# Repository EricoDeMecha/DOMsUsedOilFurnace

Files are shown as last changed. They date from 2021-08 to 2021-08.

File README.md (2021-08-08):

## DOMs: Design of a used oil furnace

Design of a used oil furnace from a mechatronics perspective. This is an improvement of what already exist and is based on the following research and implementation
## Basic description

- Pressurized oil flows through a nozzle.
- It is ignited at first and then burns on its own.
- Supercharger(Externally driven by a motor) can be added to maximize combustion.
- Ignition can be shifted from manual ignition to the use of gasoline+diesel mixture for ignition.
- Oil can be preheated also for maximum combustion

## Objectives

- High strength, and high temperature material for the design of the nozzle.(Oil atomizer)
- Automatic controlled flow of the oil.
- Automatic ignition.
- Design of a supercharger for maximum combustion(Miniblower).
- Automatic pressurizing of oil(regulator).
- Oil pre-heating
- Automatic switch over from diesel+gasoline ignition to oil burning independently.
- Smoke handling.(carbonmonoxide and smoke detectors)
- **Safety**

## Proposed designs

- Ignition system
- Nozzle
- Burning chamber
- preheating chamber

{Oil conveyance system}
## References

**Evolved used oil furnace**

Evolved used oil furnace implementation (https://www.youtube.com/watch?v=s_Ad897si6g&list=PLajok_EjFfbOb4fP-WGI7LOqIf2R0RhqM)

**Incredible burner**

Evolved used oil furnace implementation (https://www.youtube.com/watch?v=8lF8vNczoqE&list=PLajok_EjFfbMtI4L1jHQWJG012ae7ZYwm)

**JKUAT Masters Research paper**

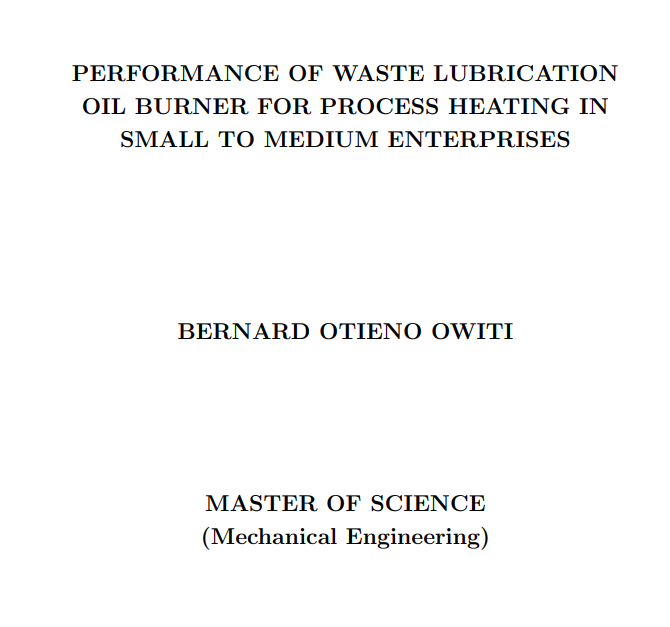
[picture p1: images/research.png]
Used oil furnace research (http://ir.jkuat.ac.ke/bitstream/handle/123456789/1776/OWITI%20B.%20O.%20MSc.%202015.pdf?sequence=1&isAllowed=y)


## Findings and miscelleneous  section
1. Miscelleneous

According to this guy here with his bad boy ...

Material evidence (https://www.youtube.com/watch?v=Qnzh19kDVuw)

* He has hit 1834 degrees by using silicon carbide in the burner and nozzle.
* He is using a thermal gun for temperature measurement and not the usual temperature industrial probe.
* Design of the nozzle
* Running at 3L/hr
* Design- simple design(Nozzle has blade with it, the blade closes the burner and can detached easily)
* Burner is also surrounded with another metal sheet to tap and direct more air directly to the flame.

2. Applications

* House warming during winter.
* Metal smelting.

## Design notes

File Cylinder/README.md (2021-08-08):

# Cylinder modelling
Modelling the cylinder thickness using internal pressure, ultimate tensile strength and factor of safety 

Installing and compiling with matplotlibcpp

## Setup

```bash
    sudo apt-get install python-pip # install pip for python 2.7
    sudo pip2 install matplotlib  # install matplotlib for python 2.7
    sudo pip2 install numpy 
    sudo apt-get install python-tk # installing tkinter for python 2.7
```

## Usage

```bash
    mkdir build  &&  g++ ../cylinderThickness.cpp  -I/usr/include/python2.7 -I/usr/local/lib/python2.7/dist-packages/numpy/core/include -lpython2.7 && ./a.out
```

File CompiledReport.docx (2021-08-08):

Conventional Oil Furnaces

Burner

Conventional designs of the burner do not gather for its maintainability. The burner is designed as a single solid attached to the nozzle. Since most furnaces operate at temperatures more than 1800⁰C, such burners burn out and become non-functional after some few operations. Due to the solid design of such furnaces, replacements of such parts require overhauling. The choice of material plays a role in the frequency of maintenance.

Nozzle

Most designs use separate nozzles for pressurized air and oil. Such a design has proven to be inefficient since smoke emissions are frequently witnessed. It also introduces complexity in the design since the pressurized air nozzle has to be placed as the measured distance from the pressurized oil nozzle and this might not always be accurate.

Ignition

Ignition for conventional oil furnaces employs a flammable burner mounted on an insulator or even soaked in a highly flammable petroleum fuel. This method is unsafe since its control is limited. The use of highly flammable petroleum fuel for ignition also makes it expensive and borderline dangerous.

Emission

Combustion of oil in a good proportion of oxygen produces carbon dioxide. During oxygen deficiencies, carbon monoxide is released. If not detected and controlled such gases can be catastrophic. Since such emissions are invisible, conventional designs of this type of furnace do not gather for such hazards.

Oil Consumption

Conventional designs are based on the workability of the design. Its efficiency is rather given very minimal attention. The use of separate nozzles for the pressurized oil and air undermines the efficiency of the design. As such, the consumption of oil is rather higher.

Assembly

Processes

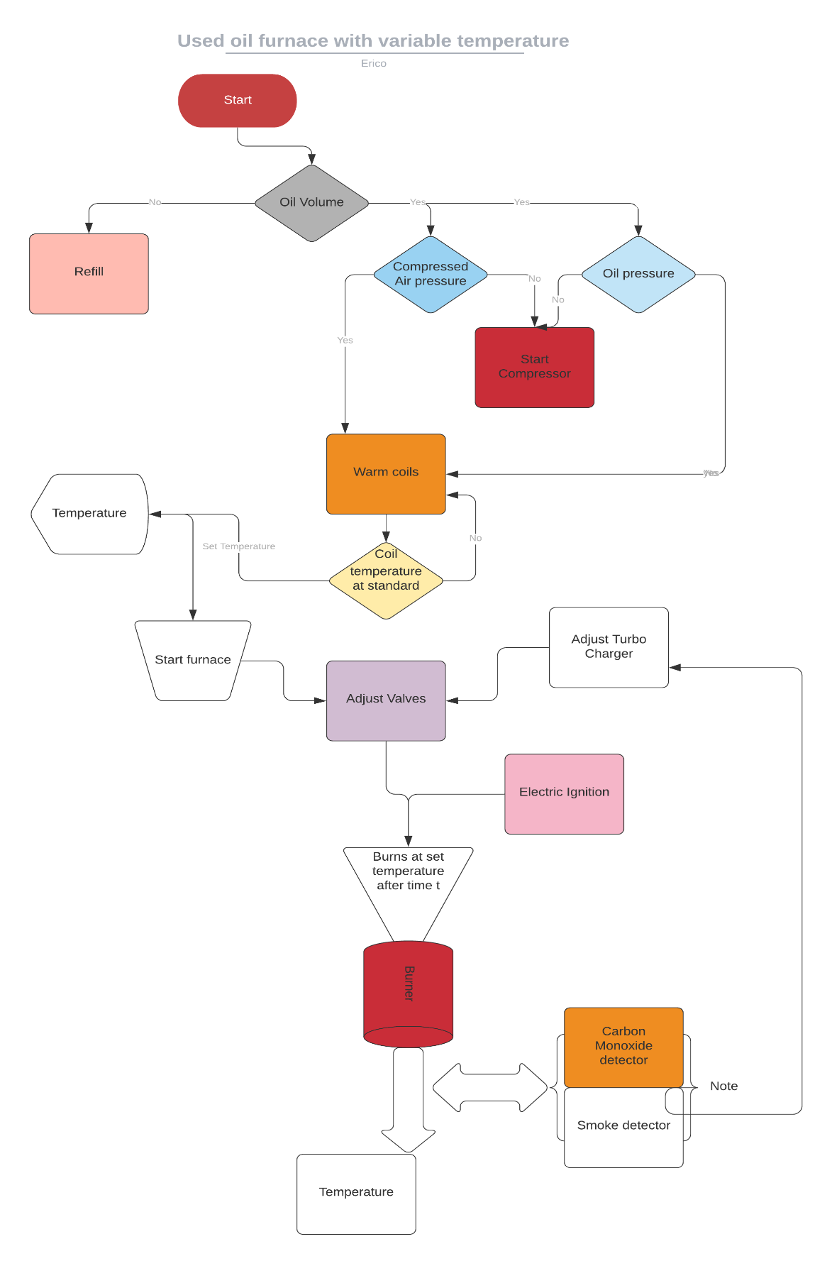
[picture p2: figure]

On powering on, the system automatically checks the volume of oil in the oil storage tank. This is determined by a level sensor installed in the tank. Depending on the volume, the system decides whether to refill the tank from an even bigger tank or raise an alert for a refill. If the required volume of oil is available the system then checks the pressure of oil in the tank and the pressure of compressed air in the air storage tank using pressure sensors. In any case, the pressure is below the required, the system automatically turns on the compressor to refill the two containers to the required pressure. Once the pressure requirements in the two containers are met, the system automatically switches off the compressors and starts warming the coils on the path of the pressurized oil to the injector. The compressor is turned on, and off to maintain constant pressure in the tank.

Once the coils warm to a standard base temperature, the user is then prompted on the interface to enter the furnace operation temperature. From this input, the system adjusts both the air and pressurized oil valves using a stepper motor connected to each of the valves. A supercharger is connected to the compressed air flow pipe through a pneumatic motor and a pneumatic gear system to magnify the speed of the airflow. It is also adjusted in proportion to the pressure along the airflow pipe. This is to ensure the maximum supply of oxygen to the combustion chamber and to reduce emissions.

The pressurized oil and compressed air mix evenly in the coaxial swirl injector. The injector is designed in such a way that it ensures oil is atomized and mixes evenly with enough amounts of oxygen. Once the flow of oil and pressurized air is steady, an electric igniter descends to the tip of the nozzle and sparks to ignite the mixture. It then retracts to a safer height since its material cannot withstand furnace temperatures.

The mixture burns at the burner. With the correct choice of material, the burner can achieve up to 1834⁰C. Around the burner are the smoke detector, carbon monoxide detector, and a thermal gun. These sensors continuously check the smoke, levels of carbon monoxide, and temperature at the output, and this information is transferred to the ECU which adjusts the supercharger, oil, and air valves to correct the values.

Cylinder modeling

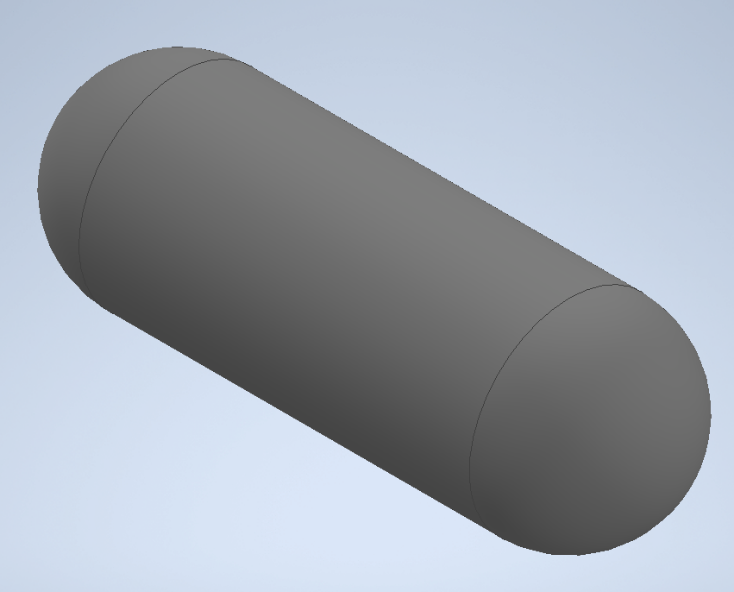
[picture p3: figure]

Fig 1.1 Cylinder

Thickness

The cylinder is designed to have to have the following dimensions:

Length: 3m

Internal Diameter: 800mm

The thickness of the cylinder has to be chosen carefully to achieve a recommended factor of safety for pressure vessels of between 3 and 6. To determine that, Clavarino’s equation is preferred to Lame’s equation since the cylinder is closed at both ends as shown in figure 1.1.

Clavarinos Equation

Clavarinos equation is used to determine the wall thickness of a cylinder. This is equation is applicable to cylinders with closed ends made of ductile materials. It is based on maximum principal strain theory.

Fig 1.2 Clavarinos Formula

Where:

P is the internal pressure, N/m²

D is the internal diameter, m

S is the allowable tensile stress, N/m²

t is the thickness of the material shell, m

µ is the poison’s ratio

Material

The material of the cylinder is chosen to meet the following objectives:

i. The material should be light (weight). This allows for bigger sizes without the limit of weight.
ii. It should be less rusty.
iii. Carbon content should not exceed a 1/8 of its total mass

Above objectives narrows down the search of the material to Carbon fiber or Fiber Glass. The amount of carbon in carbon fiber makes it a lesser attractive choice as compared to Fiber Glass even though it has a higher ultimate tensile strength. Fiber Glass is therefore chosen for the design of the cylinder.

Standard fiber glass has the following properties:

i. Ultimate tensile strength 1950-2000Mpa
ii. Poisson’s ration 0.23

Computing the ultimate thickness

To compute the ultimate thickness of the cylinder, the value of internal pressure of the cylinder can be assumed and the thickness computed. This method involves several guesses to obtain an ultimate internal pressure for a factor of safety of between 3 and 6.

Instead, a MATLAB script can be written to compute the ultimate internal pressure and thickness for a factor of safety between 3 and 6. The script is a shown below:

clc

clear

p_fos = 3; % recommended factor of safety for pressure vessels is between 3.0 - 6.0

D = 800; % internal diameter 800mm

S = 1950 * 10^6; % Ultimate tensile strength for Fiber glass

u = 0.23; % poissons ratio for fiber glass

t = [0,0.001]; % 1000th of a meter starting thickness

P = [0,0];

figure(1);

plot(P,t,"x");

i = 2;

while(1)

i = i+1;

% internal pressure

P(i)= (S*((((2*t(i-1)/D)+1)^2)-1))/((1-2*u)+(1+u)*(((2*t(i-1)/D)+1)^2));

t_fos = S/P(i); % factor of safety(fos)

% if fos is below the recommended value,break

if(t_fos < p_fos)

break

end

hold on

t(i)= t(i-1)+0.01; % 0.01 increment thickness

plot(P(1:i),t(1:i),"x");

end

title("Thickness against Internal Pressure")

ylabel("Thickness(m)");

xlabel("Pressure(Pa)")

legend("Shell Thickness vs internal pressure")

hold off

This script however, has a downside. The simulation involves computing more than 10,000 values for only a factor of safety below 30. MATLAB is super slow for this kind of computation.

An alternative C++ script can be written to speed up the computation. This is as shown below.

#include "matplotlibcpp.h"

#include <cmath>

namespace plt = matplotlibcpp;

int main(){

// declare constants

const int p_fos = 3; // recommended factor of safety for pressure vessels is between 3.0 - 6.0

const int D = 800; // internal diameter 800mm

const int S = (1950 * std::pow(10,6)); // Ultimate tensile strength for Fiber glass

const float u = 0.23; // poissons ratio for fiber glass

// prepare the data

std::vector<double> t,P;

t.emplace_back(0.001);// 1000th starting thickness

P.emplace_back(0);// 0 starting pressure

while(1){

double temp = (S*(std::pow(((2*t.back()/D)+1),2)-1))/((1-2*u)+(1+u)*std::pow(((2*t.back()/D)+1),2));

P.emplace_back(temp);

t.emplace_back((t.back() + 0.1));// increment thickness by 0.01

float _fos = (S / P.back()); // compute factor of safety

printf("%f\n",_fos);

if(_fos < 3){

break;

}

}

printf("Ultimate pressure: %f\n",P.back());

plt::figure_size(1300,768);

plt::named_plot("Thickness vs Internal pressure",P,t);

plt::title("Thickness Vs Internal pressure");

plt::legend();

plt::show();

}

The script computes both the internal pressure and factor of safety with varying thickness and stops when the factor of safety goes below 3. It then plot the relation between the thickness of the cylinder shell and the internal pressure. The plot is as shown below.

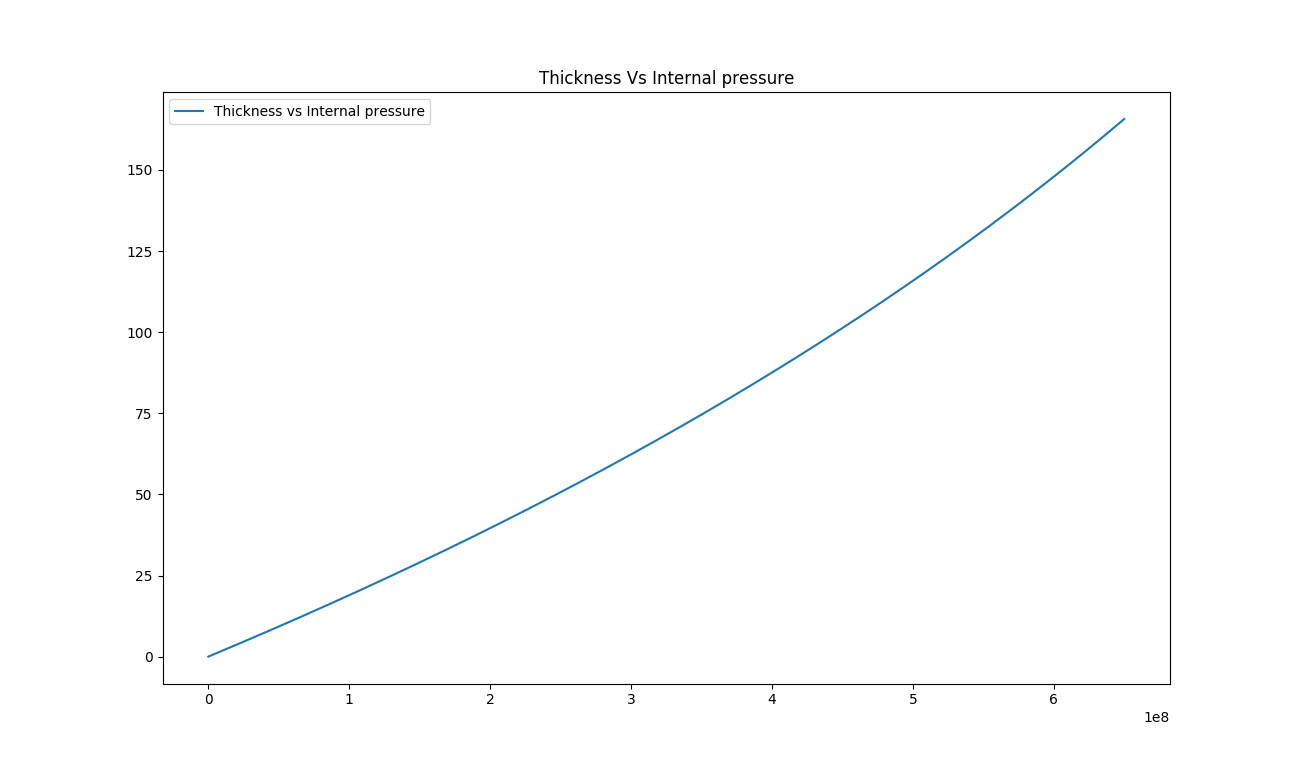
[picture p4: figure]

Fig 1.2 Thickness against Internal pressure

This shows that the relation between the internal pressure and the thickness of cylinder is linear. From the computation, it is also obtained that internal pressure of the cylinder for a factor of safety 3 is 650.042MPa. and thickness 42.075mm as shown below:

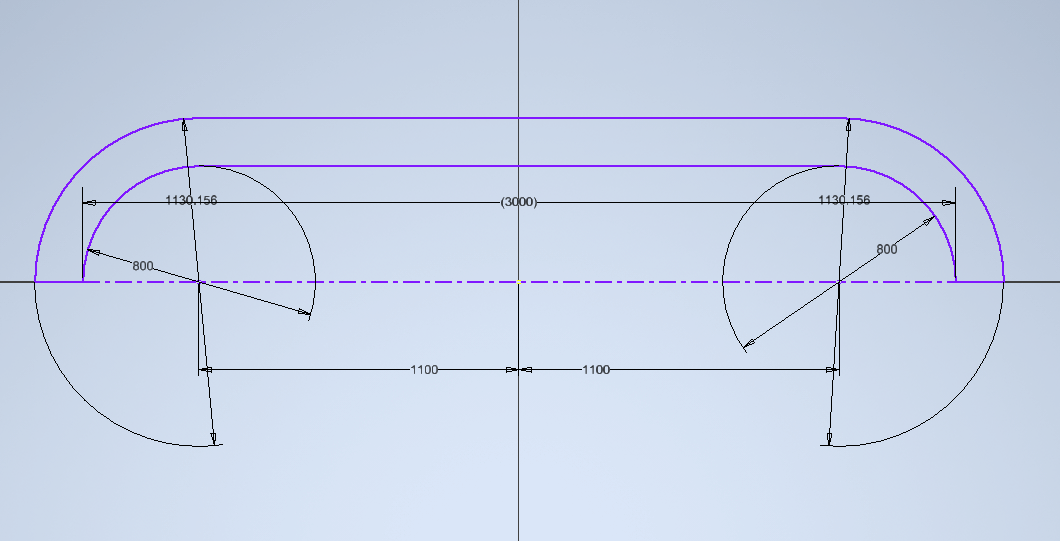
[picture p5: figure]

Fig 1.3 Actual dimensions of the cylinder

Atomizer

An atomizer is required to deliver the pressurized oil under high pressure to the combustion unit in a tiniest sprays possible. There are three viable designs for the atomizer: coaxial swirl injector, pintle injector and self-impinging injector. From the above designs the coaxial swirl injector was selected due its ease of fabrication compared to the pintle injector and self-impinging injector. The injector is expected to deliver the pressurized oil with ideal flow characteristics and atomize the fuel adequately.

Coaxial Swirl Injector

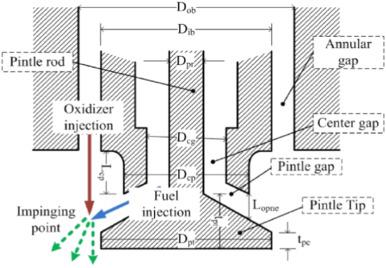
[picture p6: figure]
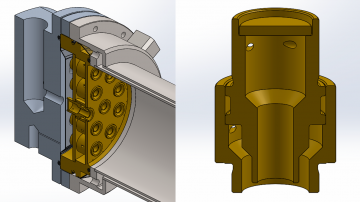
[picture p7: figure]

Fig 1,1 Coaxial Swirl Injector

Coaxial swirl injector performs the primary function of feeding oil to the combustion chamber. The design of this injector for oil furnace meets the following functional requirements;

1. The oil injector must be able to inject oil into the combustion chamber at the correct ratio and correct flow rates. For this reason the discharge coefficient of the injector must be determinable.
2. The oil injector should ensure complete mixing of oil with air to avoid undesired combustion with might result in the emission of carbon monoxide.
3. The oil injector must facilitate a primary pressure drop of between 10-20% to prevent discharged oil from flowing back into the injection system and causing an explosion.

Design

This swirl injector will consist of two primary parts; the inner element and the outer element. The two elements are placed on different levels separated by a separator plate. The inner element takes in pressurized oil tangentially which causes the liquid to swirl along the wall of the inner section. The pressurized oil enters the outer section tangentially as well and swirls along the wall of the outer element. This results in the pressurized air leaving the inner element in the shape of a cone which collides with the cone formed by the outer element. In this way the pressurized oil and pressurized air each leave each of the elements in a cylindrical manner colliding and atomizing due to the high pressure and velocity of the flow. The configuration is as displayed in figure 1.

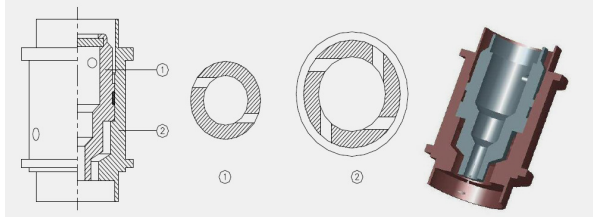
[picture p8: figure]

Fig 1.2 Swirl Injector Exploded View

This configuration meets the functional requirements of any fuel injector system .The efficiency of the injector for oil of any density can reach as high as 95%. The swirl injector has the following advantages;

1. The design is highly scalable since the assembly can be made bigger by adding the number of swirl elements in the assembly.
2. The swirl and assembly are relatively easy to machine
3. The swirl offers high atomization which is crucial for the conversion of chemical energy to thermal energy
4. The swirl element offers adjustable flow parameters allowing the assembly to create oxygen rich zones and oil rich zones.
5. Swirl elements offer the ability to vary the velocity of the fuel which can enhance the mixing of the pressurized air and pressurized oil.

The disadvantages of swirl injectors are:

1. They are a relatively new type of injector with fewer developed optimization characteristics
2. They require high dimensional accuracy for high performance

The other types of injector designs considered were;

Assembly and Fabrication

The development of the design was done by separating the assembly into five distinct parts:

1. Separator plate
2. Base plate
3. Swirler cap
4. Inner swirl element
5. Outer swirler element

Swirl Assembly

The parts were drawn on Autodesk Inventor for the 3D representation. The individual parts were then assembled. A cross section of the assembly is shown below.

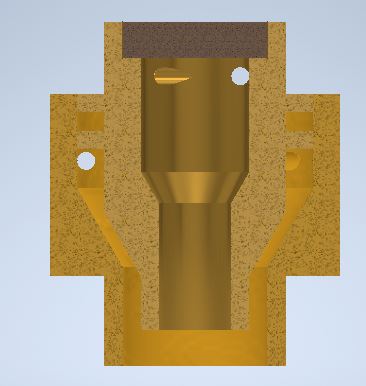
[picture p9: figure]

Fig 1.3 Cross section of the assembly

MasterCAM was then used to show the fabrication processes.

The cap was machined using a CNC lathe. The first process was facing the stock. This was followed by a rough surface turning on the outer diameter profile followed by a finishing process on the surface. The part was then cut off from the stock using a grooving tool. The tool paths are shown below:

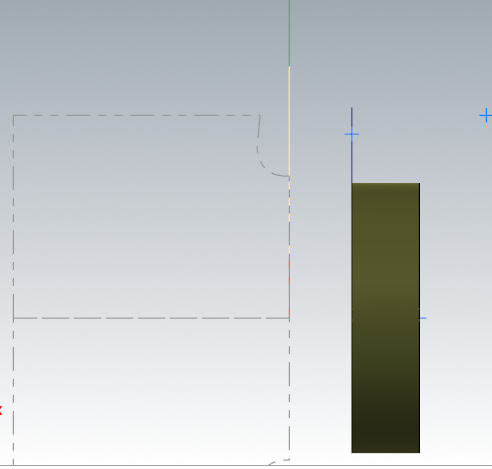
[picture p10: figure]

Fig 1.4 Cap Machining

The inner element was machined using a CNC lathe. The first process was facing using a right hand turning tool. A rough turning operation was then used to bring the dimensions to closer tolerance of the desired profile. A grooving operation was then used to machine the flanges on the profile. A grooving tool was also used to finish the tapered turning on the end of the part. A finishing turning operation was then done to bring the part to the required dimensions. A diameter 4 drill was then used to drill through the entire part. A diameter 8 drill was then used to a depth of 9mm. An internal grooving tool is then used to finalize the internal profile. The part was then cut off from the stock using a grooving tool. The holes were machined using a five axis milling machine. The figure below some of the generated tool paths.

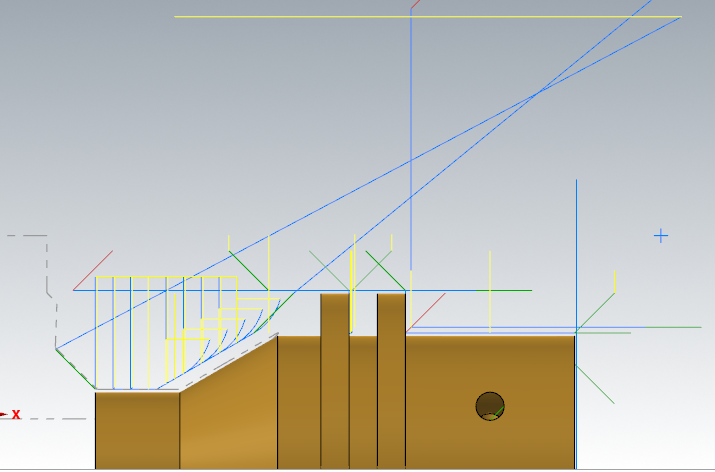
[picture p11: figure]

Fig 1.5 Inner element of the swirler

The outer element was machined using a CNC lathe. The first process was facing. This was followed by a rough turning operation on the profile. A grooving tool was then used to machine the end on the profile where there is a diameter change. The outer element was then finalized with a finishing turning operation. For the internal profile a drill of diameter 8 is passed through the entire stock. THis is followed by a drilling with a 12 mm drill to a depth of 12.12mm. The internal profile is then finalized by an internal turning operation. The part was then cut off from the stock using a grooving tool. The holes were machined using a 5 axis milling machine.

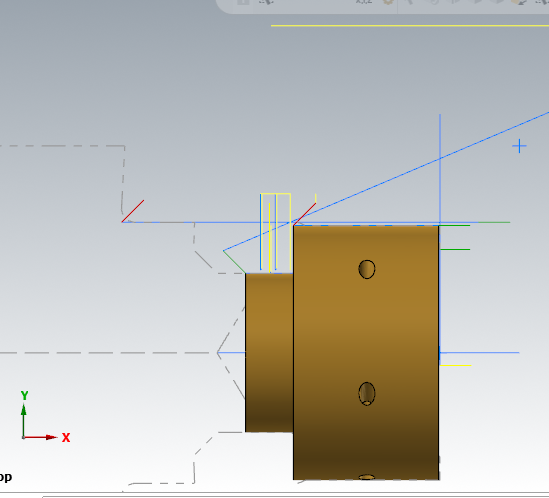
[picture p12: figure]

Fig 1.6 Outer element of the swirler

Base plate

The stock of this part was as defined:

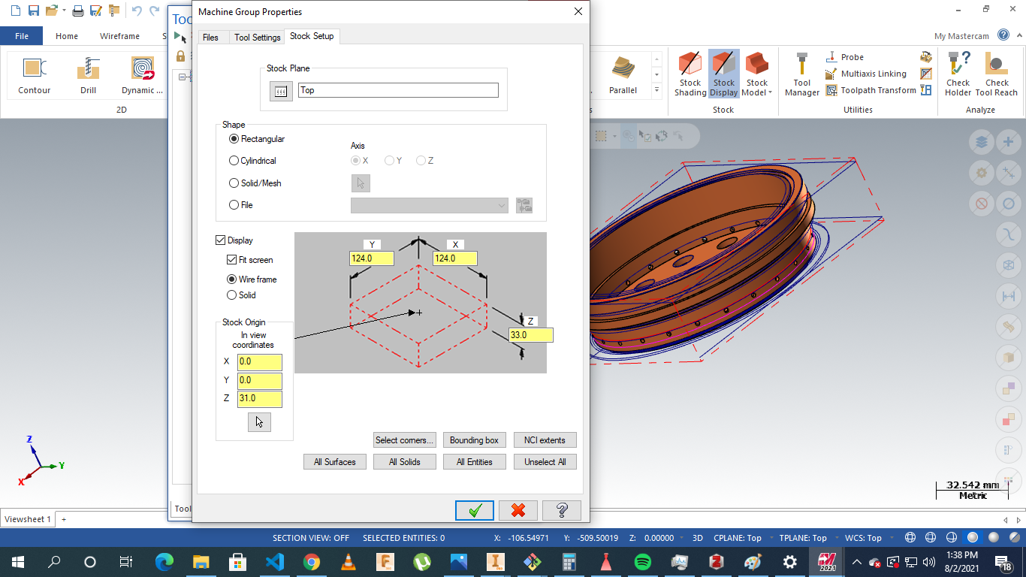
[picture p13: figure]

Fig 1.7 Base plate machining

The operations were to conducted on a five axis milling. The processes involved include: facing, contour milling drilling slot milling and multi-axis drilling.

The parts were milled as the material to be used was brass.

Operations are highlighted below:

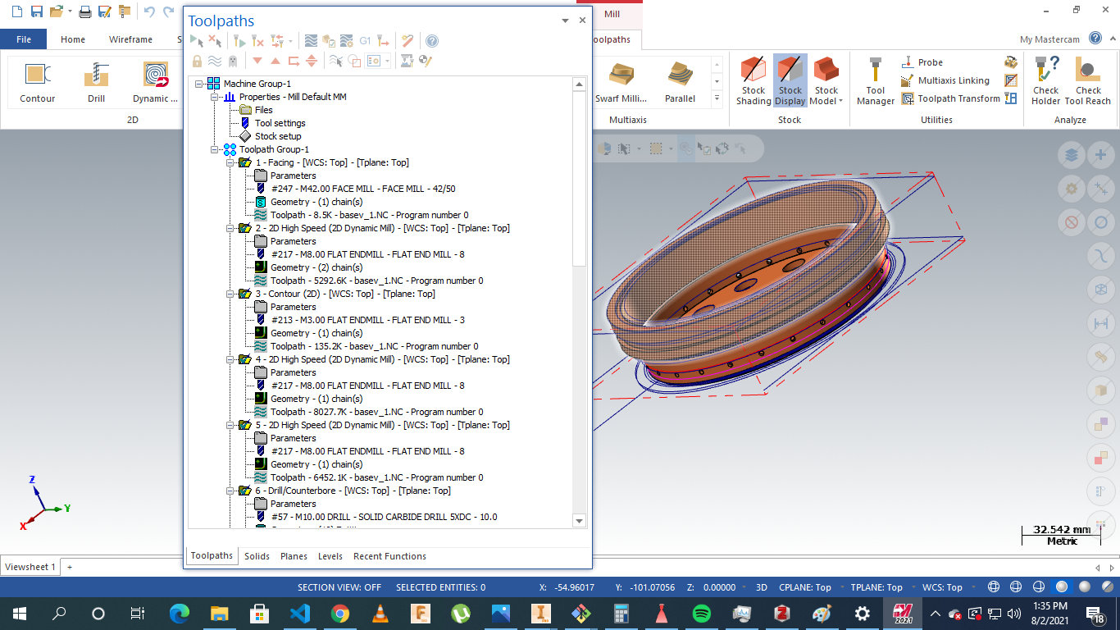
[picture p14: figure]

Fig 1.8 Base Plate total operations

Separator plate

The stock was as defined:

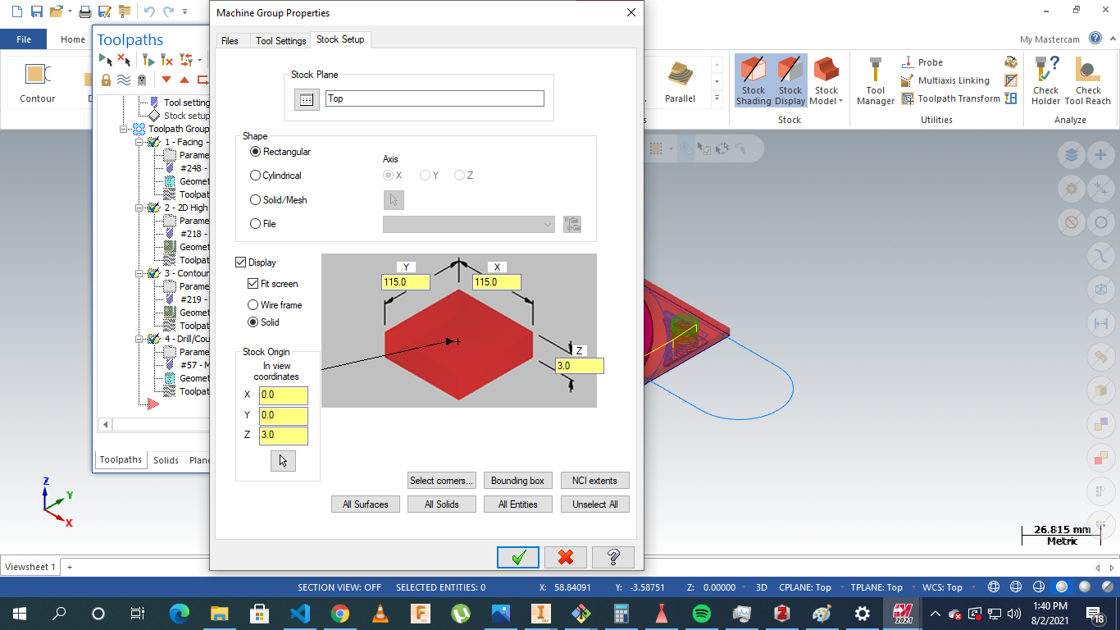
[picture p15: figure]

Fig 1.9 Separator plate stock Setup

The operations involved: facing, drilling,contouring and parting.

The processes were as displayed :

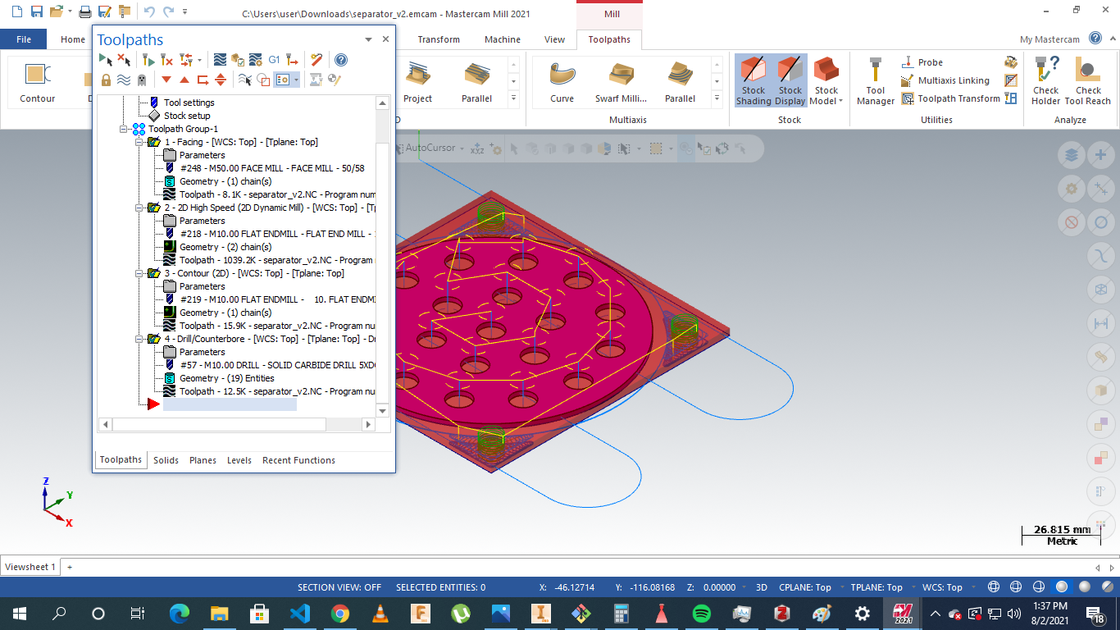
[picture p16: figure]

Fig 2.0 Stock Plate Machining Instructions

References

L.-J. Yang and Q.-F. Fu, ‘Theoretical Investigation on the Dynamics of a Gas-Liquid Coaxial Swirl Injector’, (https://www.zotero.org/google-docs/?tOBzsF)J. Propuls. Power (https://www.zotero.org/google-docs/?tOBzsF), vol. 27, no. 1, pp. 144–150, 2011. (https://www.zotero.org/google-docs/?tOBzsF)

H. Belal, A. Makled, and M. Al-Sanabawy, “Vaporization-controlled simplified model for liquid propellant rocket engine combustion chamber design,” IOP Conference Series: Materials Science and Engineering, vol. 610, p. 012088, Oct. 2019, doi: 10.1088/1757-899X/610/1/012088.

Edge, E. (2021). Clavarinos equation thick-walled cylinders of ductile material Calculator and formula. Retrieved 7 August 2021, from https://www.engineersedge.com/calculators/clavarinos_equation_thickwalled_cylinders_15620.htm

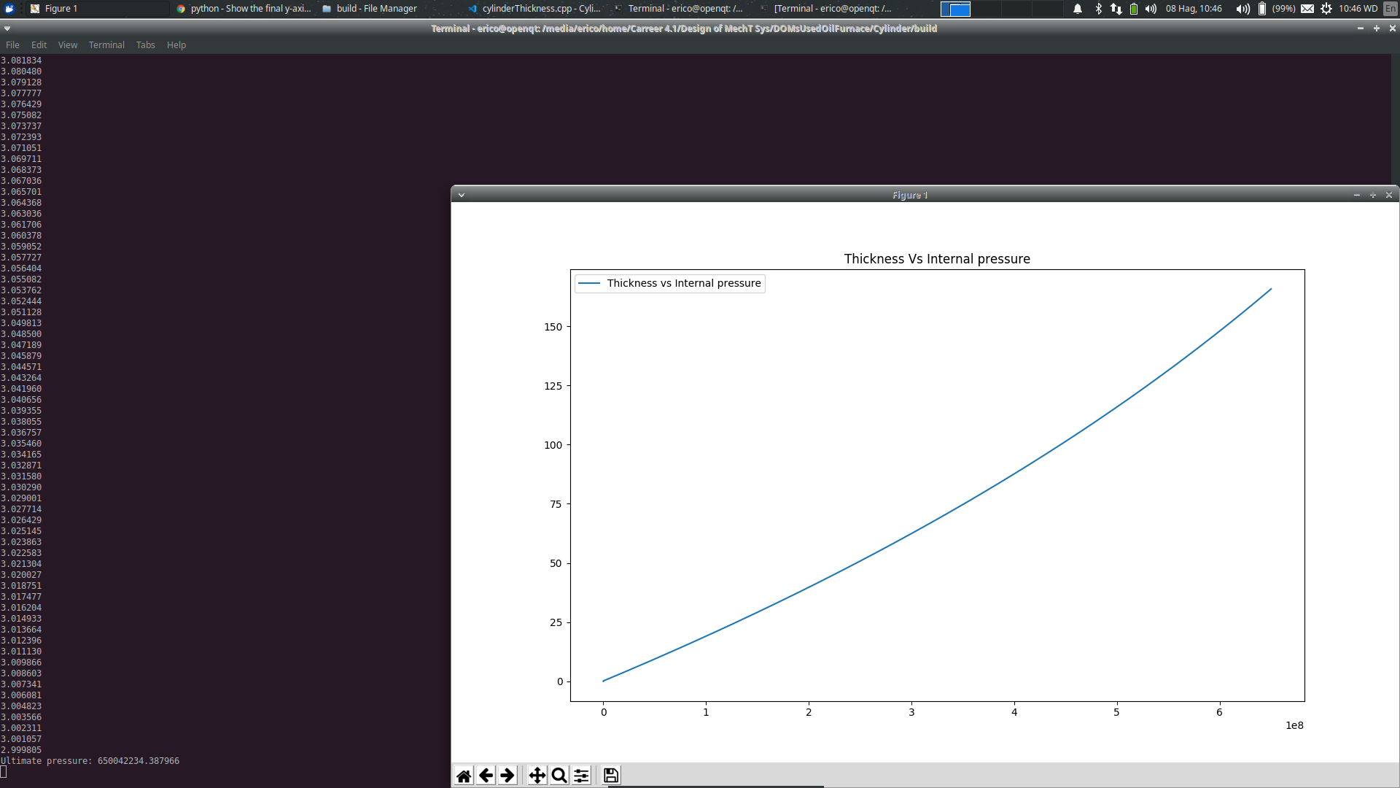
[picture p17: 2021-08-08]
images/ultimatePressure.png

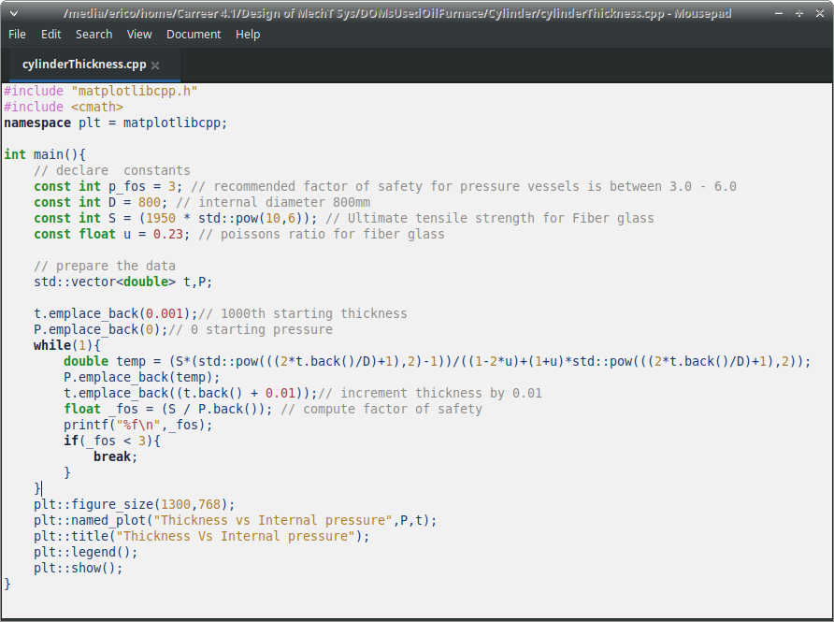
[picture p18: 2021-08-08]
images/CylinderThickness.png

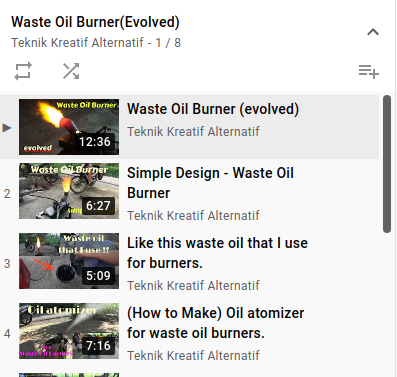
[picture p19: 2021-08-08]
images/playlist.png

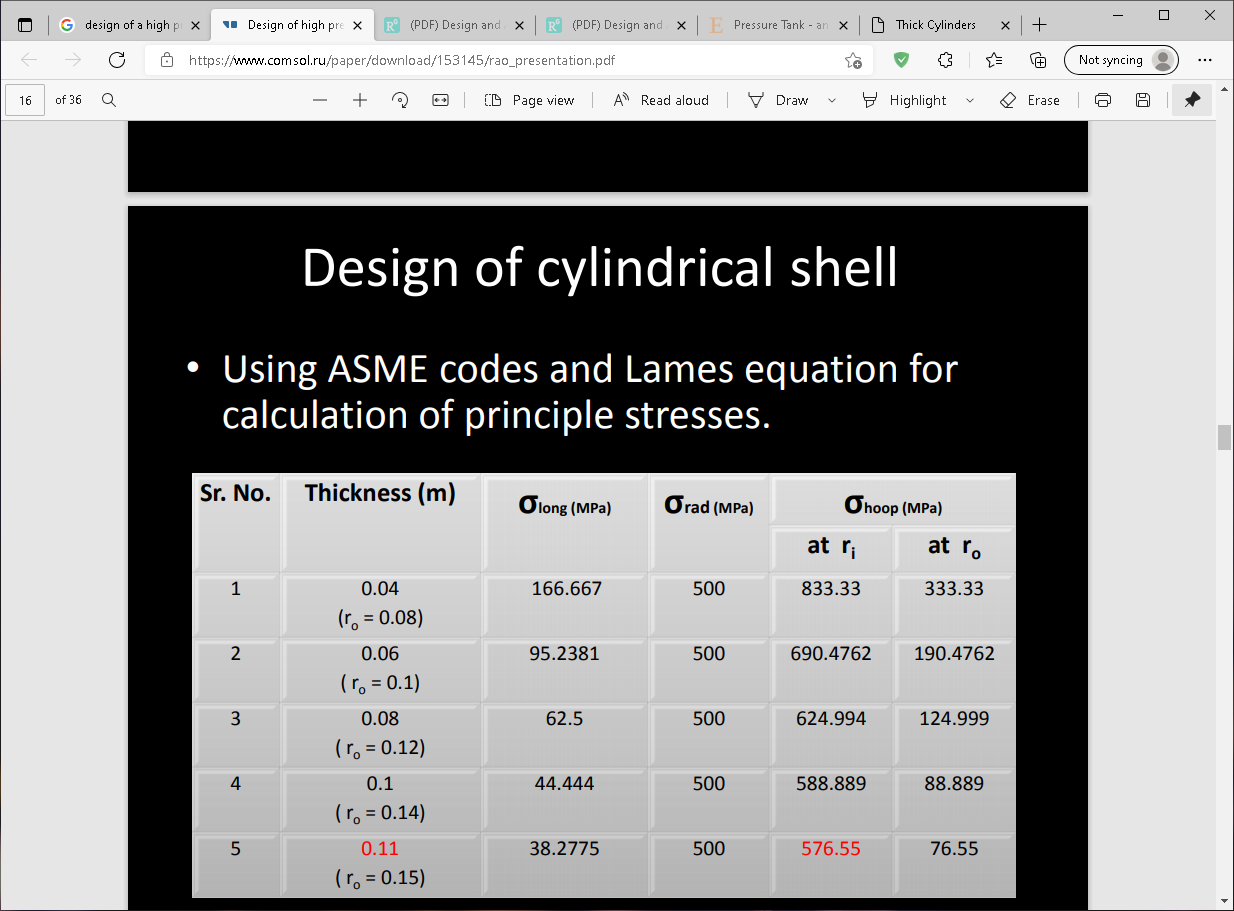
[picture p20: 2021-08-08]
images/ASME Applied.PNG

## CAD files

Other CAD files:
Cylinder/Design/Cylinder.ipt
Cylinder/Design/OldVersions/Cylinder.0001.ipt
nozzleSwirlInjector/DesignCADCAM/CAD-CAM/Parts and assemblies/base_single.ipt
nozzleSwirlInjector/DesignCADCAM/CAD-CAM/Parts and assemblies/basev_1.ipt
nozzleSwirlInjector/DesignCADCAM/CAD-CAM/Parts and assemblies/cap.ipt
nozzleSwirlInjector/DesignCADCAM/CAD-CAM/Parts and assemblies/injector assembly.iam
nozzleSwirlInjector/DesignCADCAM/CAD-CAM/Parts and assemblies/inner element.ipt
nozzleSwirlInjector/DesignCADCAM/CAD-CAM/Parts and assemblies/outer element.ipt
nozzleSwirlInjector/DesignCADCAM/CAD-CAM/Parts and assemblies/separator.ipt
nozzleSwirlInjector/DesignCADCAM/CAD-CAM/Parts and assemblies/separator_single.ipt
nozzleSwirlInjector/DesignCADCAM/CAD-CAM/Parts and assemblies/separator_v2.ipt
nozzleSwirlInjector/DesignCADCAM/CAD-CAM/Parts and assemblies/single-elemnt -assembly.iam
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

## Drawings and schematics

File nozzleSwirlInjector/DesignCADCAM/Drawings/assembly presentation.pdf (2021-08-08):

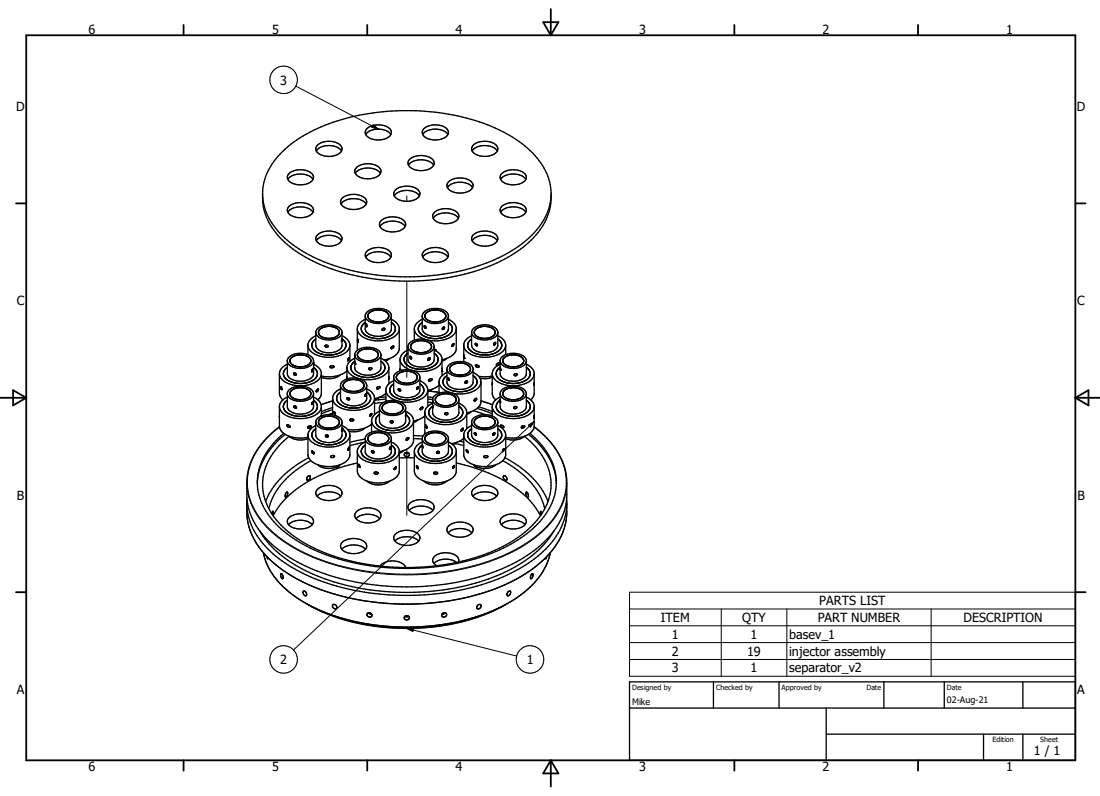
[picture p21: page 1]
Mike; 02-Aug-21; Designed by; Checked by; Approved by; Date; 1 / 1 Edition; Sheet Date PARTS LIST; ITEM; QTY; PART NUMBER; DESCRIPTION; basev_1; injector assembly; separator_v2 1

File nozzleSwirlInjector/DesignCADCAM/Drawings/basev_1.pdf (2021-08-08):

1

2

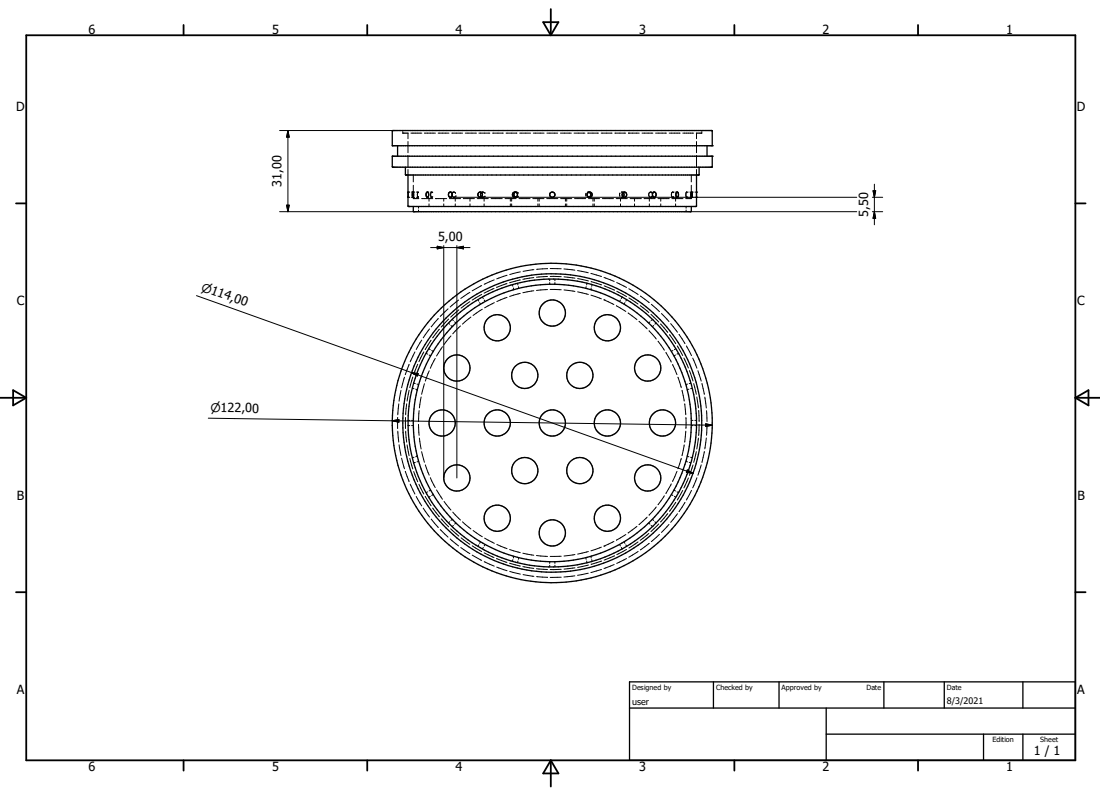
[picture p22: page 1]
user; Designed by; Checked by; Approved by; Date; 1 / 1 Edition; Sheet Date ⁵,50

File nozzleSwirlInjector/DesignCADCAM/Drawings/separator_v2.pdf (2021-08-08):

1

2

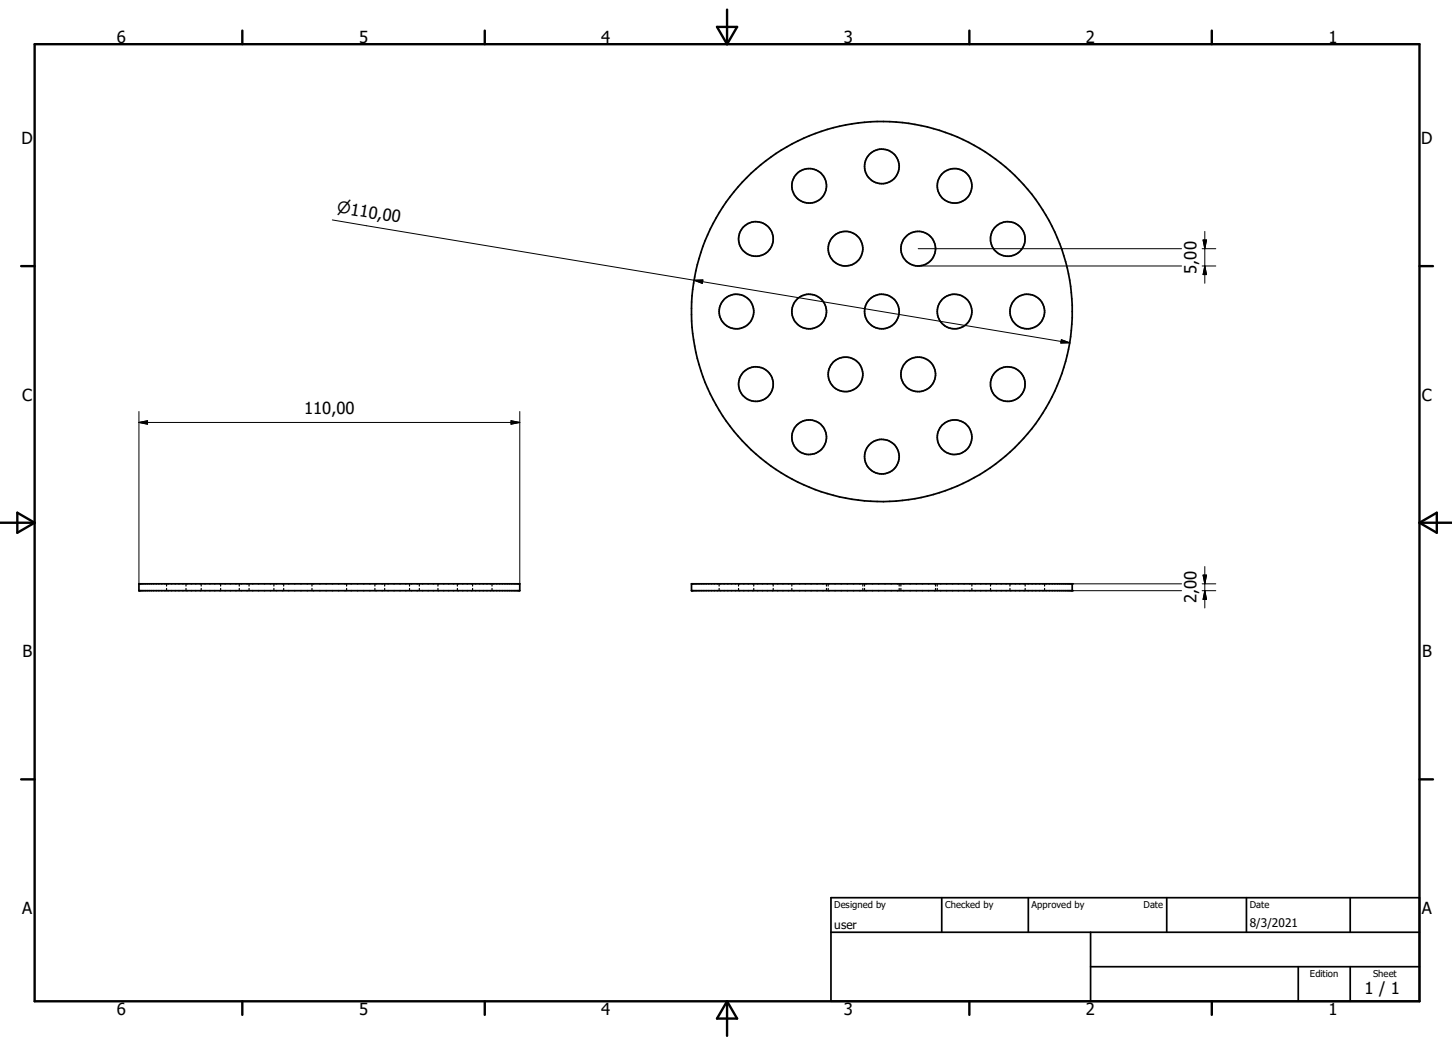
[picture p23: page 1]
user; Designed by; Checked by; Approved by; Date; 1 / 1 Edition; Sheet Date

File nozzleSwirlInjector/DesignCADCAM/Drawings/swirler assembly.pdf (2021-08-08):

1

2

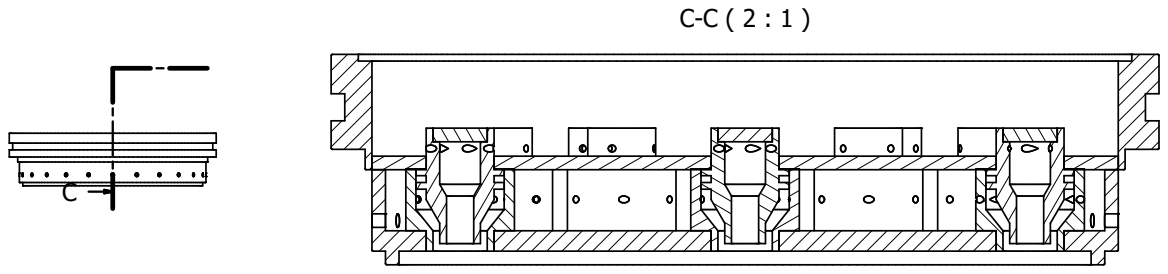
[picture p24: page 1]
swirlerassembly; user; Designed by; Checked by; Approved by; Date; Edition; Sheet

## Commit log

2021-08-05 [README] added material selection findings and applications
2021-08-08 [Cylinder] complete with report and design
2021-08-08 [cylinder] cylinder designed and optimal pressure determined
    [Cylinder.0001.ipt, Cylinder.ipt]
2021-08-08 [Nozzle] Design and report completed
    [base_single.ipt, basev_1.ipt, cap.ipt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]
2021-08-08 [Assembly] Added a flow chart and TODOS for conventional furnaces
2021-08-08 [assembly] added conventional designs
2021-08-08 Introduction and heating elements design
